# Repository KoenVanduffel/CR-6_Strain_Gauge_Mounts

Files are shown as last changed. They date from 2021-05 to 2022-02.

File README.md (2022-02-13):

- [Creality CR-6 SE & MAX extruder and hotend collection mounting directly to the strain gauge](#creality-cr-6-se---max-extruder-and-hotend-collection-mounting-directly-to-the-strain-gauge)
  * [Daughterboard](#daughterboard)
  * [fan mount](#fan-mount)
  * [Extruders:](#extruders-)
    + [Orbiter **V1.5**:](#orbiter---v15---)
    + [Mjolnir:](#mjolnir-)
    + [Bondtech LGX Lite:](#bondtech-lgx-lite-)
  * [Hot ends:](#hot-ends-)
    + [Dragon](#dragon)
    + [Mosquito](#mosquito)
    + [MicroSwiss for Creality CR-6](#microswiss-for-creality-cr-6)
    + [Stock hotend](#stock-hotend)

# Creality CR-6 SE & MAX extruder and hotend collection mounting directly to the strain gauge

## **I am in the process of moving this repo over to the PrusaPrinters.org repository of prints, for the latest updates please check the https://www.prusaprinters.org/social/211289-k2van/collections/114416 collection page. I link the relevant page in every subdirectory.**

A collection of hot end and extruder combinations for the Creality CR-6 SE and CR-6 MAX is provided in this repo.

```For ease of use the structure has been changed with every possible hotend in a directory followed by directories with the different extruders.```

All extruder / hot-end combinations are mounted directly onto the strain gauge without any connection to the carriage. The aim is to avoid the issue of the extruder pushing down on the strain gauge and causing variation in layer height in the typical gantry mounted direct drive setups. An added benefit is that the mount will prevent the strain gauge from vibrating as it blocks downward movement. Only the upward movement to enable bed measurement is allowed. Mounting the extruder this way ensures the shortest possible filament path which is exactly the aim of a direct drive setup. Only the Hemera and alike designs achieve even shorter filament paths.

There are a few gantry mounted direct drive setups available that try to avoid this pushing down on the strain gauge issue by installing a washer.

The disadvantage is that the stock hot end cover does not fit any longer (A series is planned which will work with the stock hot end cover, however the filament path will inevitably be slightly longer).

## Daughterboard
The daughterboard needs to be mounted on its own mount as the stock mount interferes with the extruder. A separate mount can be found in the daughterboard directory. 3 versions are available: one to mount the PCB directly to the mount (on standoffs) and two others that allow/require you to use the plastic OEM mounting plate/cover to mount the board to the plate.  The first mount places the board too low for the LED to safely clear your models and bed clips.
NOTE: Whichever of these daughterboard mounts you use, the LED will no longer be positioned to shine below the nozzle unless you design and make your own modifications to address that.

## fan mount
A series of fan mounts using generic 5015 or 5020 blower fan mounts optimized for each hotend is provided. With thanks to Alex for the idea of the "ears" the fan shroud design has been greatly improved and cooling efficiency of this 5015 fan is very high (enabling lower speed / quieter operation).
The fan mount has to be printed in PETG, ASA, ABS PCTG or another higher temperature filament. PLA will simply melt as its too close to the hotend.

## Extruders:
For this principle to work we need an extruder that has less than 9 mm space needed behind its filament path or it will not fit between the gantry and the hot end entrance. Two extruders have been selected:
### Orbiter **V1.5**:
> The Orbiter is the highest performing extruder I have tested. With PETG in combination with a high flow Dragon I get up to 600 mm3/min (or 25 mm3/s) extrusion speed with just 1.5% deviation versus no resistance at all.
>The Orbiter has a high gear ratio which is beneficial for extrusion as it will improve acccuracy significantly. It has been found that this can cause noise when using the filament unload function of the Community Firmware. The speed is set so high that the extruder will run at nearly 800 rpm. This will not damage the motor but some people have reported that it makes a lot of noise (probably skipping of the motor).

### Orbiter **V2.0**
>The Orbiter V2.0 is currently NOT supported! It might be an upgraded extruder versus the V1.5 however it does not fit on the strain gauge. The drive gears have been turned around which makes it collide with the back carriage plate.

### Mjolnir:
> An extruder using the internals of a BMG extruder. For this any BMG extruder or clone can be used. Also a set of the internals of a BMG extruder is sufficient. The performance is similar to a genuine BMG extruder or its clone variant. I measured an extrusion drop of 5 to 6% with PETG in identical circumstances and filament as the test with the Orbiter. Not as good as the orbiter but still more than sufficient for standard or even slightly higher print speeds.

### Bondtech LGX Lite:
> The all new Bondtech LGX Lite extruder (NOT THE REGULAR LGX, that one too bulky to fit the CR-6). A mount is modeled but untested for now as I do not own an LGX lite. This could well become the highest performance option as its lighter and more compact than the Orbiter 1.5 and  can be mounted closer to the strain gauge bringing the center of mass of the whole hotend assembly closer to the strain gauge thus avoiding vibration of the strain gauge upon higher accelerations.
> Extrusion performance is obviously untested by me but should be equal to or better than the Orbiter.

## Hot ends:
The hot ends chosen all have mount screw holes on the top making them rather easy to mount. Also are they significant all metal upgrades to the stock hot end.
The extruder - hotend mount blocks can be printed in any filament however PETG, PCTG, ASA or ABS are preferred over PLA.

### Dragon
> both high flow and standard flow

### Mosquito
### MicroSwiss for Creality CR-6
### Stock hotend
<br/>
Just a couple of examples:

<img src="images/README/CR-6 Dragon & Orbiter mount with stator fan.png" alt="CR-6 Dragon & Orbiter mount with stator fan" width="60%" />

![CR-6 stoch hotend and Mjolnir extruder](https://user-images.githubusercontent.com/13643644/121425564-d613ab00-c972-11eb-9b16-f10bbce3bcb8.png)

![Mosquito   Orbiter mount 2](https://user-images.githubusercontent.com/13643644/121426032-65b95980-c973-11eb-9b75-b8b25f1e59a7.png)

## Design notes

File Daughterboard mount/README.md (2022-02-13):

### Updated daughter board mount and ribbon cable management

The daughterboard mount  and ribbon cable holders can now be found on PrusaPrinters.org

[PrusaPrinters](https://www.prusaprinters.org/prints/126838-cr-6-direct-drive-dragon-hf-sf-and-orbiter-v15-mou)

The original hot end cover and daughter board mounts are not useful any more as the extruder & hot end mounts come in the way (except for some of the Bowden setup's). Therefore these companion daughter board mounts and cable management have been made. 


The updated mount supports the whole board and has a clamp to hold the lowest rather flexible part of the ribbon cable. This works in conjunction with  the ribbon cable clamps and ribbon cable holder (which clips over the pulley housing of the X-axis motor).



For the daughterboard mount there are additional options. One to mount the with the original plastic back to enable the use of the blue LED. and one with a right angled approach to enable easier cable management (requires somewhat longer than stock heater and thermistor wires). The daughter board mount V1.1 (still available) was only a small mount just enough to hold eth daughter board in place.

The part fan shroud has been moved out of this directory into the different hot end directories. The different sizes of heater blocks ask for slightly different designs for the different hot ends.

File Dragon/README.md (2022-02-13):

# Dragon hotends

The Dragon hotend designs including the daughterboard and part fan shourds for the Orbiter have been moved to the PrussaSlicers page.

[PrusaPrinters](https://www.prusaprinters.org/prints/126838-cr-6-direct-drive-dragon-hf-sf-and-orbiter-v15-mou)

**The Dragon Orbiter V1.5 has been updated to fit both the high and standard flow version. The older version is still available in the high flow and standard flow directories.

The latest V4 mount for Dragon + Orbiter V1 now has a connection of top and bottom on the left side making the mount even more sturdy and probably more durable. A small cutout has been added to grant access to the screw of the daughterboard mount for ease of maintenance.
These updates are to be ported to the other designs soon.**

The Dragon hotend (TriangleLabs and Phaetus version are nearly identical and fit both) has a strong reputation of being a reasonably priced high qualtiy hotend. Personally i prefer the high flow version as it hasn't shown any of the disadvantages sometimes attributed to a high flow hotend but does have the advantage of being capable of melting a lot of plastic.

# Part fan shrouds

The part fan shroud in this directory fits all extruder versions, high flow as well as standard flow.

2021-11-28 update: 
5015 and 5020 versions of the fan shroud are now available
The "ears" have been opened up as it was found not needed to close as much as earlier versions did. This further improves cooling efficiency.
A secondary channel pushing some air directly downwards below the fan shroud has been added as this region was getting less cooling thus fixing the reduced overhang capability in that region.

CR-6 5020 part fan shroud

CR-6 5020 part fan shroud 2

CR-6 5020 part fan shroud 3

CR-6 part fan shroud simulation

On the 2 section analysis the internal flow redirector is visible. A blower fan typically gives a higher output flow towards the circumference versus the inside The devider helps correcting that. The second divider lets some air flow to just below the shroud as this area gets too short cooling time when the hotend moves to the left.

The simulation picture shows the effect ot the ears in avoiding a "shadow" directly to the left ot the nozzle. Basically they make the airflow converge again.

I ran the Teaching tech 4-way overhang test to validate my design: https://www.thingiverse.com/thing:3167063





This test produces overhangs up to 80°. Up to 60° the overhangs are perfect, 70° is perfectly useable and even 80° would be useful if no other way is found and some sagging is accepted (PLA @200 °C, 0.4 mm nozzle, 0.2 mm layer height, 0.45 mm line width, 25 mm/s exterior walls). I tested slower print speeds but that produces lesser results. Using the 5015 the results are less good when printing faster. The 5020 manages up to 50 mm/s with no/barely loss in overhang quality. Beyond 50 mm/s outer layer speed a 10° lesser overhang maximum should be used.

### Print settings:

- layer_height = 0.2
  layer_height_0 = 0.24
  line_width = 0.45
  infill_line_width = 0.4
  
  bottom_layers = 5
  top_layers = 5
  wall_line_count = 5
  
  material_bed_temperature = 85
  material_print_temperature = 230
  
  infill_pattern = gyroid
  infill_sparse_density = 20
  
  cool_fan_speed = 40
  cool_fan_speed_max = 75
  cool_min_layer_time = 10
  cool_min_layer_time_fan_speed_max = 20
  cool_min_speed = 10
  
  z_seam_corner = z_seam_corner_weighted
  z_seam_type = back
  z_seam_x = 235

Adjust temperature and fan setting if using another filament than PETG

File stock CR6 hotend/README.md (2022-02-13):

The stock CR-6 hotend and Orbiter design can now be found on PrusaPrinters.org.

[PrusaPrinters](https://www.prusaprinters.org/social/211289-k2van/collections/114416)

The part fan cooling mount featured here is compatible with both Bowden and direct drive setup.

Last modification adds a small cutout because some 5015 fans have rather large clips to close the body that were interfering with the mount.

CR-6 part fan mount stock hotend v3

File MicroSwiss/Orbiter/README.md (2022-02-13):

# MicroSwiss and Orbiter

The mount has been moved to PrusaPrinters.org. The new version is identical to the one for the stock hotend.

[PrusaPrinters](https://www.prusaprinters.org/prints/132112-cr-6-direct-drive-stock-or-microswiss-hotend-orbit)

This mount is menat to install the Orbiter extruder and MicroSwiss CR-6 hotend in direct drive mode directly onto the CR-6 SE or CR-6 Max strain gauge.

There is not hotend in the render file as MicroSwiss hasnt released a CAD file of the extruder. If anyone has a CAD file please notify me so I can integrate it in the render for convenience.

Many thanks to @ritchiedc on the CR-6 discord for providing me the necessary measurements to adapt the existing mounts to the MicroSwiss hotend.

CR6 MicroSwiss hotend and Orbiter extruder mount v1

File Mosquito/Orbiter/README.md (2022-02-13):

# The Mosquito plus Orbiter mount direct to the strain gauge

The Mosquito and Orbiter mount has been moved to PrusaPrinters.org

[PrusaPrinters](https://www.prusaprinters.org/prints/129781-cr-6-direct-drive-mosquito-standard-and-magnum-and)

CR6 Mosquito and Orbiter mount on the strain gauge

The mount for the Mosquito - Orbiter combination to the strain gauge. The file marked injection molding inserts is meant to be used with the typical IM inserts. The preferred inserts are the regular hot melt inserts as they give a much stronger part.

The regular 5015 part blower fan mount does not fit! A modified version to fit the wide Mosquito heater block is incuded here.

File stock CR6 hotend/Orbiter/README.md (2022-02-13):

# Mount block to mount the Orbiter extruder to the stock CR-6 hotend.

The stock CR-6 hotend and Orbiter design can now be found on PrusaPrinters.org.

[PrusaPrinters](https://www.prusaprinters.org/social/211289-k2van/collections/114416)

CR6 stock hot end and Orbiter extruder mount v1

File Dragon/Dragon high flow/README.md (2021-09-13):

# Dragon high flow hotends
The Dragon high flow hotend (TriangleLabs and Phaetus version are nearly identical and fit both) has a strong reputation of being a reasonably priced high qualtiy hotend. Personally i prefer the high flow version as it hasn't shown any of the disadvantages sometimes attributed to a high flow hotend but does have the advantage of being capable of melting al lot of plastic.

There are 3 extruder options:
* Bowden setup
* Orbiter **V1.5** (high performace large gear extruder)
* Mjolnir extruder (3d printed BMG clone)

A version using the Voron Galileo Clockwork extruder is in the planning. The Galileo Clockwork uses the internals of the Orbiter and will thus perform very similar.

`There have been multiple requests to make a Bondtech LGX or Superfly version. These extruders are however too bulky and simply don't fit in the space available. To mount these they have to be lifted over the carriage back plate which will increase vibrations as the momentum on the strain gauge is increased.`

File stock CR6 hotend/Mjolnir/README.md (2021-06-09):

CR-6 stoch hotend and Mjolnir extruder

Mount the Mjolnir extruder directly on the CR-6 SE and MAX hotend.

There are 2 "front" files. One has a flat bottom, the other one an extension to guide the Bowden tube. Please try what suits best.

The Boden tube length will be critical as it has to press down on the hot end to avoid cloggs but not too much so as not to deform and cause a restriction to the filament path. The Bowden tube should be 55 mm.

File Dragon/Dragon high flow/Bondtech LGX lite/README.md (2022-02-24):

# Bondtech LGX Lite & Dragon high flow
This mount has been updated and moved to PursaPrinters.org:
https://www.prusaprinters.org/prints/137422-cr-6-direct-drive-lgx-lite-and-dragon-mount-to-the

LGX lite Dragon

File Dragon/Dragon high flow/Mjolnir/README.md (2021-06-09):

cr6 Mjolnir extruder Dragon v1

The Dragon extruder is a popular after market all metal extruder. This page host the mounts to combine the Dragon with the Mjolnir extruder (Bondtech BMG derivative).

Needed parts:
 Dragon hotend: 
   https://nl.aliexpress.com/item/1005002629698126.html
   BMG extruder internals:
    https://nl.aliexpress.com/item/4000021186440.html
Both the extruder and the hotend are available from different sources as well. Watch out there are some Dragon clones where the top BMG mount cannot be removed. These will not fit.

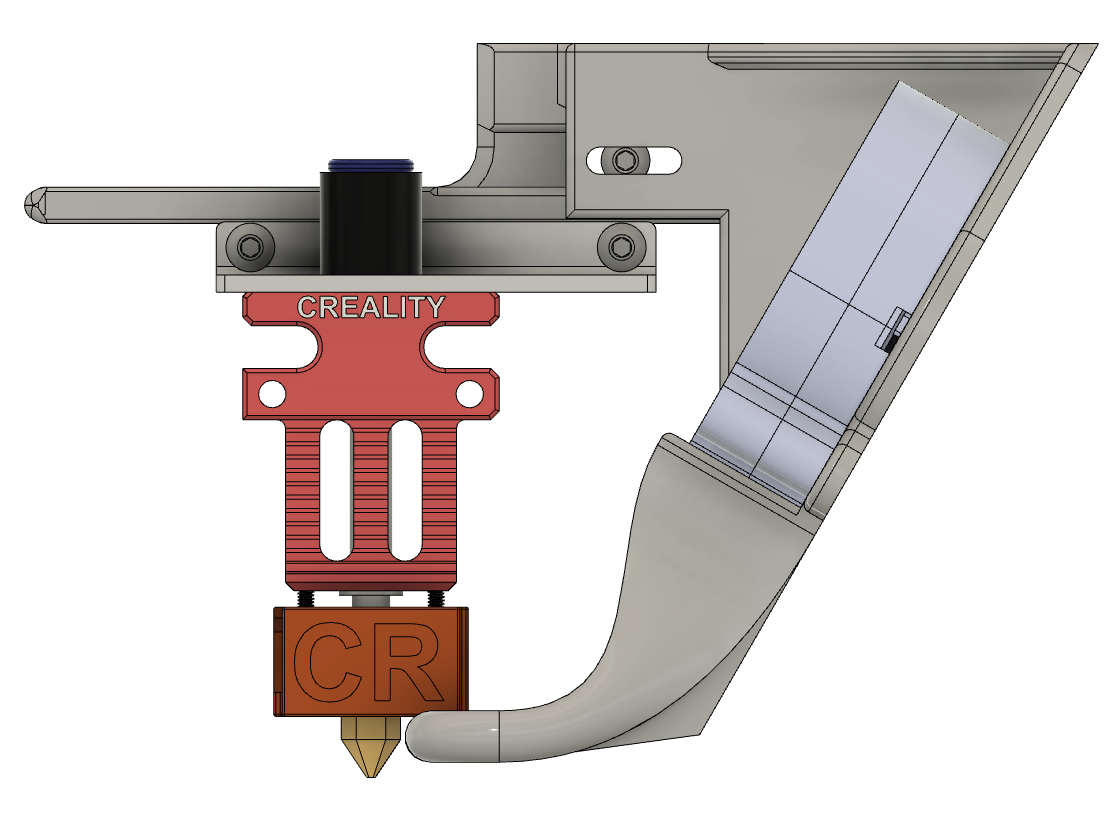
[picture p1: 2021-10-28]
stock CR6 hotend/images/README/CR-6 part fan mount stock hotend v3.png

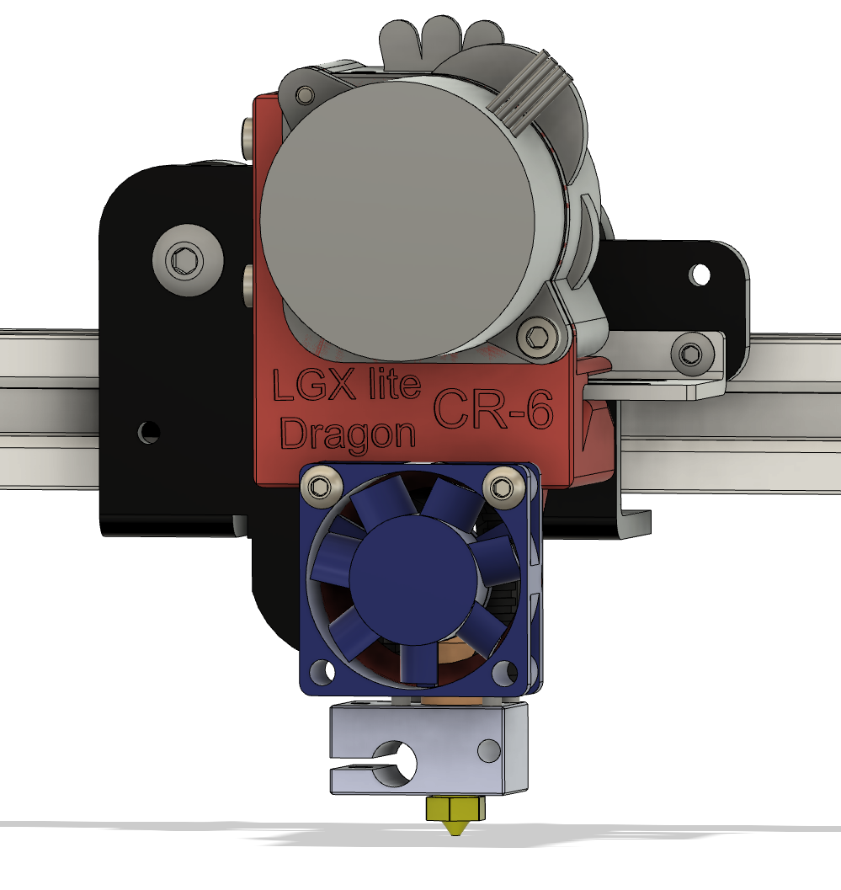
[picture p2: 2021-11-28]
Dragon/Dragon high flow/Bondtech LGX lite/LGX lite & Dragon.png

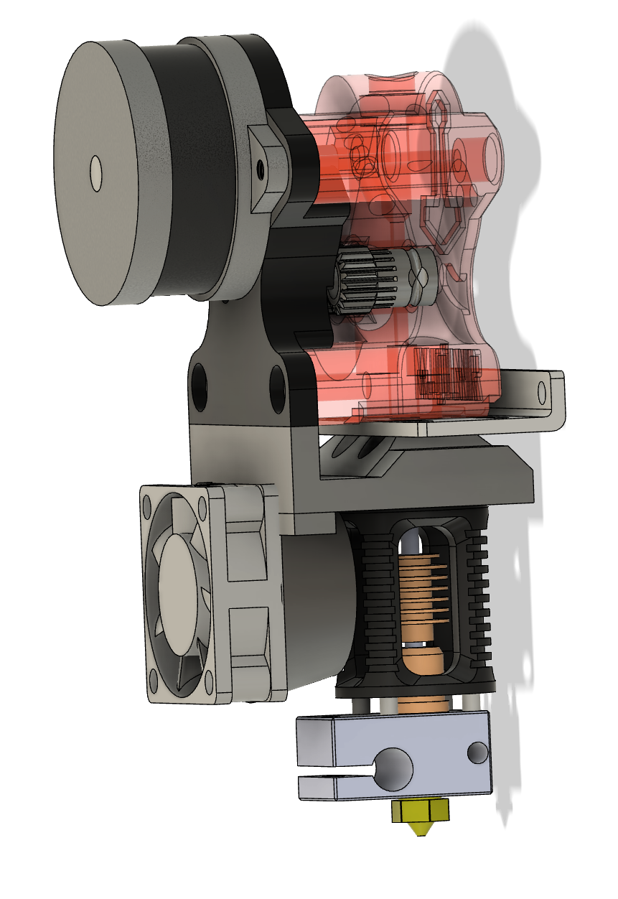
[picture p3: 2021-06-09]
Dragon/Dragon high flow/Mjolnir/cr6 Mjolnir extruder & Dragon v1.png

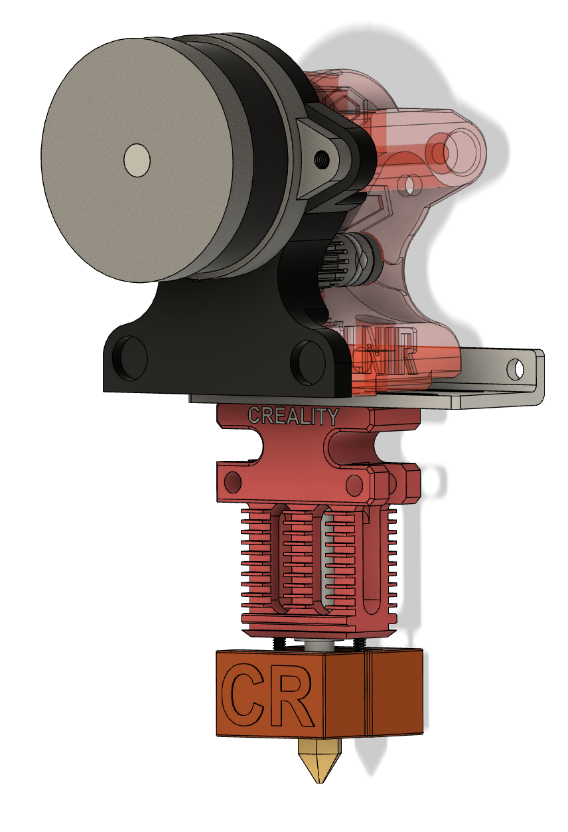
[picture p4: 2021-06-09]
stock CR6 hotend/Mjolnir/CR-6 stoch hotend and Mjolnir extruder.png

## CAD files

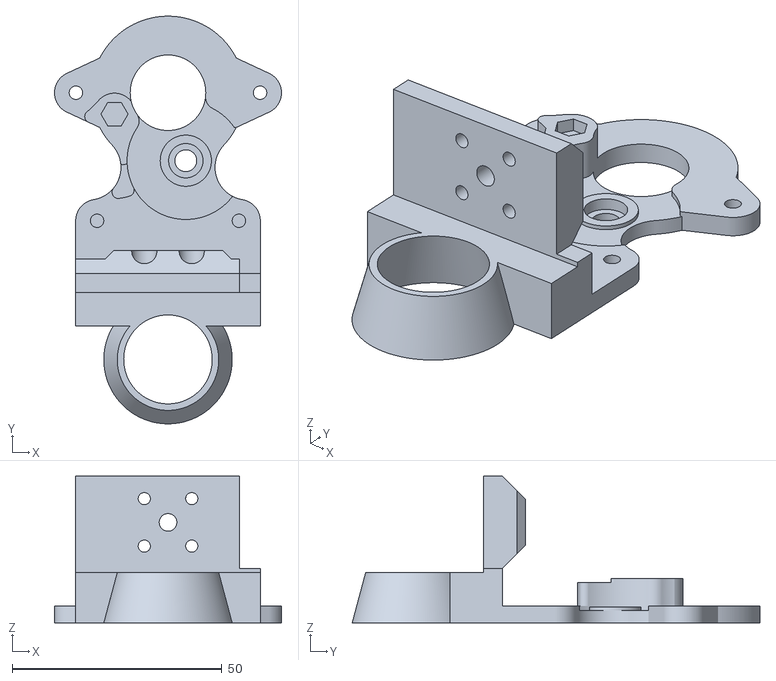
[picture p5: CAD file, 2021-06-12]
Dragon/Dragon high flow/Mjolnir/CR-6 Dragon standard flow & Molnir extruder M3 4.6mm hot melt inserts back.stl
54.1 x 97.2 x 35.0

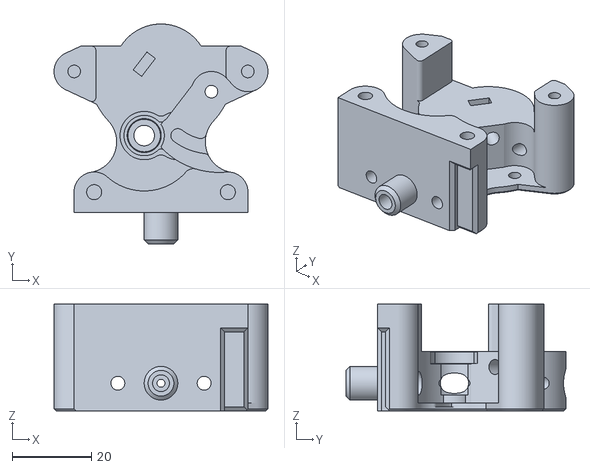
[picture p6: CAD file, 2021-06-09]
stock CR6 hotend/Mjolnir/CR-6 stock hotend and Mjolnir extruder front with filament path.stl
54.1 x 55.6 x 27.0

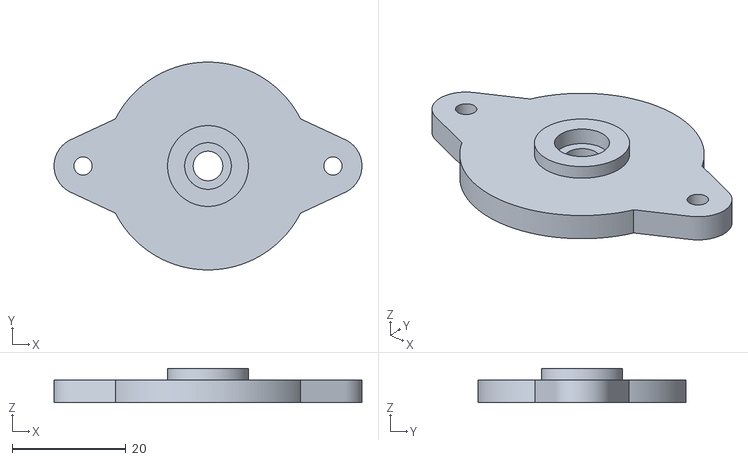
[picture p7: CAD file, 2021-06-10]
Dragon/Dragon high flow/Mjolnir/Motor Dummy_1x_SN.stl
54.1 x 36.5 x 6.00

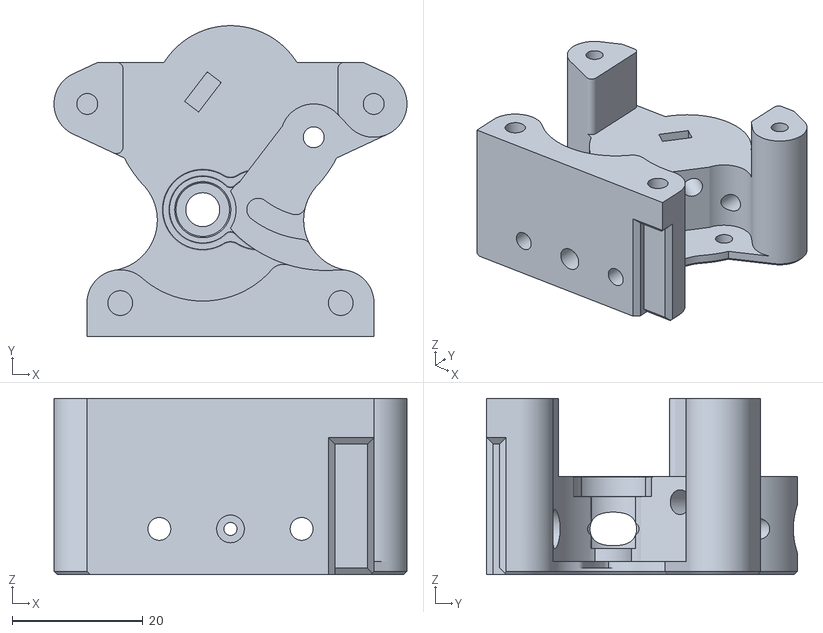
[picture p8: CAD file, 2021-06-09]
stock CR6 hotend/Mjolnir/CR-6 stock hotend and Mjolnir extruder.stl
54.1 x 47.6 x 27.0

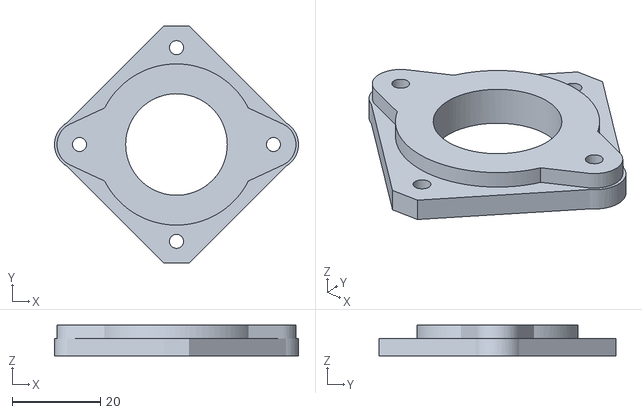
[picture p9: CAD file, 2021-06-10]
Dragon/Dragon high flow/Mjolnir/Nema 17 adapter.stl
55.2 x 53.7 x 7.00

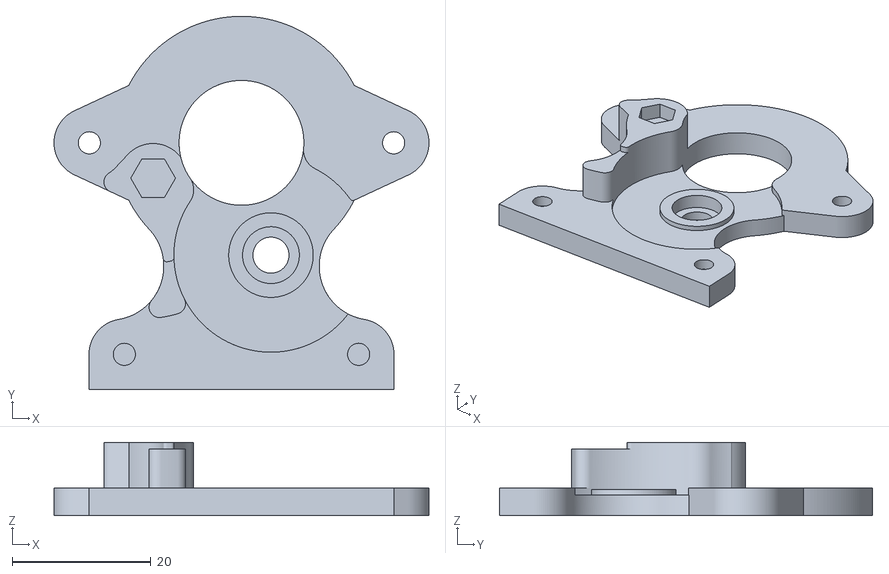
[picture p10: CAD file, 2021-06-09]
stock CR6 hotend/Mjolnir/CR-6 stock hotend and Mjolnir extruder back.stl
54.1 x 53.9 x 10.6

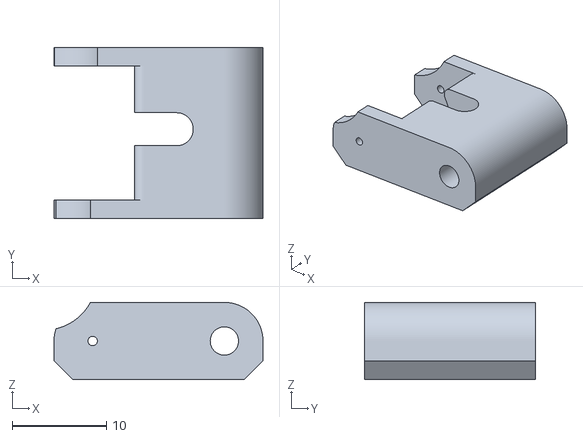
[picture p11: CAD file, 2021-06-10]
Dragon/Dragon high flow/Mjolnir/31_mjolnir lwx latch_1x_SN_BN.stl
22.2 x 18.2 x 8.20

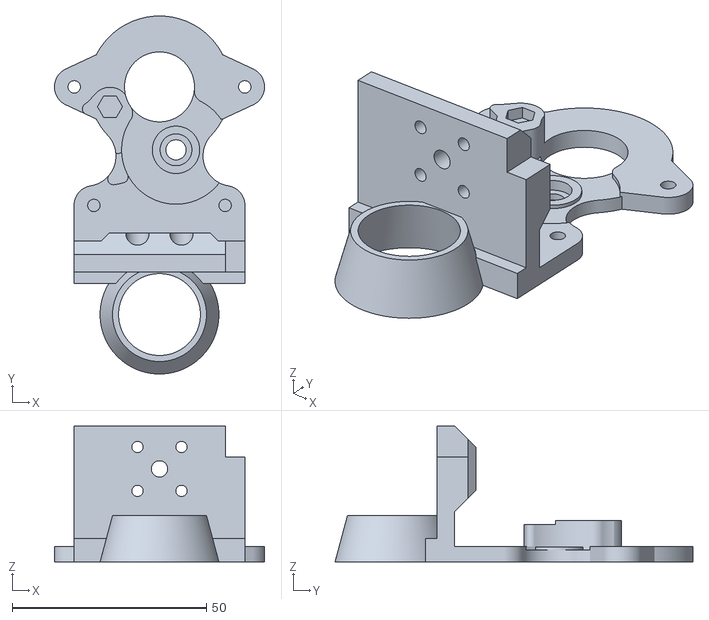
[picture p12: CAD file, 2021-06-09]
Dragon/Dragon high flow/Mjolnir/CR-6 Dragon high flow & Mjolnir M3 4.6mm hot melt inserts back.stl
54.1 x 92.2 x 35.0

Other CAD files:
Dragon/Dragon high flow/Mjolnir/CR-6 Dragon & Mjolnir hot melt inserts front.stl

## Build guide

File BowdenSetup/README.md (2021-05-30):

# Creality CR-6 SE and CR-6 MAX Bowden mounted Dragon hotend.

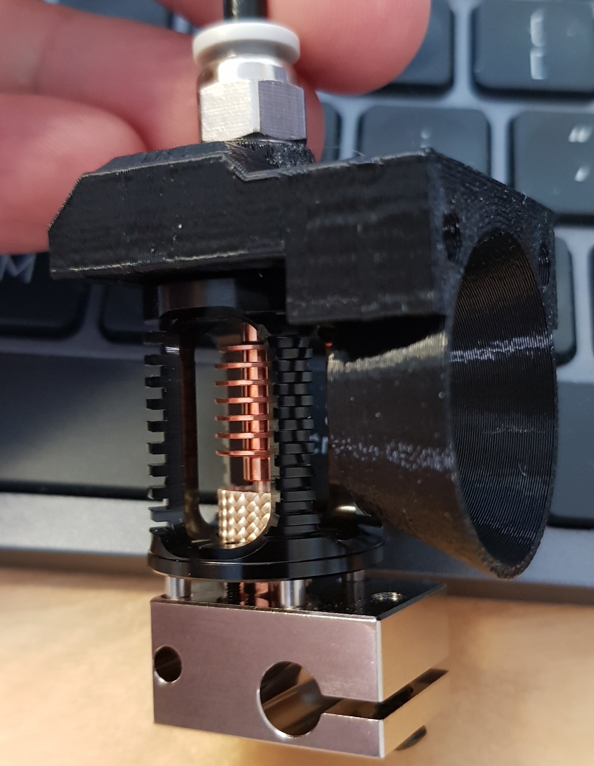
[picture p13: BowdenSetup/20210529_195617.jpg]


## 4 variants are available:
	
	High flow Dragon with the fan shroud slightly higher mounted to avoid cooling the extended heatzone
	Standard flow Dragon with fan shroud mounted lower
	
	For both versions there is a choice between a version with:
    M3 bolts and nuts
    M3 bolts and hot melt inserts. For the fan 2 3mm long M3 hot melts are sufficient,
		longer is possible. For the mount to the strain gauge 7 mm long M3 hot melts are recommended.

### Print prefereably in PETG or other high Tg material. The bottom of the fan shroud might sag when printing in PLA.

## Printing:

	0.16 mm layer height
	activate "Use Adaptive Layers" with maximum variation and step size 0.04 mm and Topography size 0.2 mm
	0.44 mm line width
	4 walls, top and bottom layers
	Activate "Alternative Extra Wall" in the walls menu of Cura
	20% Gyroid infill (Gyroid provides good vibration damping)
	No supports, the holes and screw tread print good enough on my CR-6
	Print at high temperature (240 or 245 °C for PETG)
	You might ocnsider upping the flow rate to 105% to get maximum part strenth. Experiment with this setting if needed.

## Mounting:
	
	Mount the Dragon with the supplied bolts
	Mount the fan with 16 or 18 mm M3 bolts
	Mount the assembly to the strain gauge with 10 mm M3 bolts
	
	The 10 mm Bowden coupler is screwd directly in the platic thread. Do not overtighten!

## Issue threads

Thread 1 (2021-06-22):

How to connect the mosquito to your design?

deuse-x, 2021-06-22:
Hi.
I just made your great design for the CR- SE Mosquito_And_Orbiter

I think I will have to buy some inserts to connect it to the strain gauge.

But I can not find a way to connect the Mosquito to your design.
The holes for it are way to big.
I can't put a insert in.
Can you help please?

Thank you for your design and letting us use them.

KoenVanduffel, 2021-06-22:
Both sets of holes should get melt inserts. I will check whether I made a mistake in the sizing.

I don't own a Mosquito (clone) myself so haven't been able to test it.

⁣Get TypeApp for Android

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

deuse-x, 2021-06-22:
> Both sets of holes should get melt inserts. I will check whether I made a mistake in the sizing. I don't own a Mosquito (clone) myself so haven't been able to test it. ⁣Get TypeApp for Android
> […](#)
> On Jun 22, 2021, 15:39, at 15:39, deuse-x ***@***.***> wrote: Hi. I just made your great design for the CR- SE Mosquito_And_Orbiter I think I will have to buy some inserts to connect it to the strain gauge. But I can not find a way to connect the Mosquito to your design. The holes for it are way to big. I can't put a insert in. Can you help please? Thank you for your design and letting us use them. -- You are receiving this because you are subscribed to this thread. Reply to this email directly or view it on GitHub: #1

Thank you.

I just bought these  https://www.amazon.co.uk/threaded-embedment-assortment-ultrasonic-embedding/dp/B08KVWYTN1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

Hope they are the right kind.
I will post pics.

Thank you again

KoenVanduffel, 2021-06-22:
These are not actually hot-melt inserts but injection molding inserts (they often get sold as hotmelt inserts unfortunately). You can either get the real ones (these are the ones I bought https://nl.aliexpress.com/item/1005001553234012.html) or i adjust the hole sizes but that will be tricky as there is very little room to the filament path. Hence If you reprint you will probably have to drill the filament hole to get the Bowden tube trough.
I have a set of the ones like you bought, they don't have M2.5. However if extrapolating from the M2 the shaft of the M2.5 ones should be 3.3mm. The holes are 3.2 and print 3.0 (due to the molten plastic moving inward a little). If you happen to have a 3.2 or 3.4 mm drill you could increase the hole size a little.
I uploaded a version with the increased hole size to accommodate the IM inserts. I have not increased the size of the holes for the Orbiter or strain gauge as those seem to be a bit more size tolerant when I understand you correctly.
I will include a bit more text and a video from CNC Kitchen to explain this better.

deuse-x, 2021-06-23:
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

Thank you so much.

I just bought the ones from AliExpress.
It's the 300 set I got.

KoenVanduffel, 2021-06-23:
I don't have a real YouTube channel. I just posted a 10:24 Benchy today which is my first ever YouTube post https://m.youtube.com/watch?v=kOTIyuHyYVc

deuse-x, 2021-06-23:
> I don't have a real YouTube channel. I just posted a 10:24 Benchy today which is my first ever YouTube post https://m.youtube.com/watch?v=kOTIyuHyYVc
> Quality is quite poor as it was just the Raspberry cam recording it...

WOW that does move fast!!!

Never seen anything like it  :)

Well done dude.

deuse-x, 2021-06-23:
> I don't have a real YouTube channel. I just posted a 10:24 Benchy today which is my first ever YouTube post https://m.youtube.com/watch?v=kOTIyuHyYVc
> Quality is quite poor as it was just the Raspberry cam recording it...

Sorry to bother you.

But which set did you buy off aliexpress?
I know nothing about these. I've just noticed that there are all lengths and sizes.

Thanks again.

KoenVanduffel, 2021-06-23:
When I bought them i didn't know anything either :). I bought set nr 4-20 which I though were the sizes I would use most. i bought a larger bag of M3x4.5x3.0 and M3x4.6x7.0 from this seller (watch out he also has M3x3x4.2 so the same screw thread but smaller outside diameter, in itself no issue but you need to make the holes the correct size) https://nl.aliexpress.com/item/4000958639502.html
There are however quite a lot of sellers, probably also local ones. the thing to watch out for is the narrower tip and 2 rings with angled nudges. The IM ones have straight nudges which is OK but they are at the sides which makes mounting difficult and pushed the plastic in front if you push then in too quickly. So be slow, let the plastic melt and gravity should do the work.

deuse-x, 2021-06-23:
> When I bought them i didn't know anything either :). I bought set nr 4-20 which I though were the sizes I would use most. i bought a larger bag of M3x4.5x3.0 and M3x4.6x7.0 from this seller (watch out he also has M3x3x4.2 so the same screw thread but smaller outside diameter, in itself no issue but you need to make the holes the correct size) https://nl.aliexpress.com/item/4000958639502.html
> There are however quite a lot of sellers, probably also local ones. the thing to watch out for is the narrower tip and 2 rings with angled nudges. The IM ones have straight nudges which is OK but they are at the sides which makes mounting difficult and pushed the plastic in front if you push then in too quickly. So be slow, let the plastic melt and gravity should do the work.

I will get the 4-20 one for starters.

I'm old and my mind is not working right  :)
So sorry about all this.

KoenVanduffel, 2021-06-23:
No problem, this also teaches me where i can improve if only in the explanation part (which i still have to make for the biggest part anyway).

Closed 2021-08-24.

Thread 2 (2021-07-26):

Not really an issue. Can I confirm the strain gauge still functions?

RobboCop, 2021-07-26:
Hi,

Sorry for making this an issue, I don't have much experience on GitHub, so I didn't know another way to ask this question.

From what I can see of the CAD, the mount will surround both sides of the strain gauge. I am guessing that this would render the strain gauge redundant? It's possible that you have allowed sufficient room for the gauge to still function, but I can't tell from just eyeballing it.

Further, your speed boat video starts after the homing process has been completed, so I couldn't tell from that.

The video was impressive though! Did you need to add active cooling for the stepper motors? I know that some people have complained that theirs get quite hot.

ritchiedc, 2021-07-26:
The strain gauge still functions. The mount does restrict the gauge from deflecting down by design but it still deflects upward when the nozzle contacts the bed.

KoenVanduffel, 2021-07-26:
Thx Ritchie, I can't explain the principle any better. Blocking the downward movement is the aim of the design as it dampens vibration. The upward movement is left free for the bed measurements to function indeed.

KoenVanduffel, 2021-07-26:
I didn't comment on the motors. I use a BTT board and Klipper sets a lower current when not moving which keeps the motors much cooler. The  move current was increased to 1A, hold 350mA for the Y axis and 850mA 350mA for the X axis respectively.

RobboCop, 2021-07-26:
Thanks for the replies gents, that was the news I was hoping for.

Yes there are several separate mods just to prevent the strain gauge moving down to stop the hot end from oscillating/bouncing. So that is a feature really, just couldn't tell if it would still deflect upwards.

Looks like I have some parts to buy then. I got a Prima all metal hot end, but the actual hot end is fastened to the heat break with a tiny grub screw. Applying practically any torque to the steel grub screw simply strips the thread from the alloy heat break... Looks like the micro swiss design is very similar, so I don't really want to buy another setup and be faced with the same issue. Thinking I might just go all in and opt for a setup similar to yours

KoenVanduffel, 2021-07-26:
I have no experience with the prima3d or MicroSwiss hotends. They both seem to perform well in printing but might have the disadvantages you describe.

I have ran the Mjolnir Dragon combintion for a while before switching to the Orbiter Dragon combination. The Orbiter extruder has more consistent flow in the higher flow ranges (less than 1% drop in extrusion up to the point where the hotend can't melt the plastic any more) compared to the BMG designs (5 to 7% drop). As long as you are not printing with large nozzles or more than 100 mm/s you won't notice this difference.

Bear in mind however that the Dragon also bas a few small screws. The screws and hotend body have however proven to be of good quality for me as I haven't damaged any of them even though I have fastened and loosened them a few douzen times when developping the mounts.

KoenVanduffel, 2021-08-24:
Clarified

Closed 2021-08-24.

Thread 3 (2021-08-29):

Heat creep with PETG

RobboCop, 2021-08-29:
**Describe the bug**
So, I have assembled this setup with a Dragon highflow and Orbiter. Works the goods with PLA ~210C, I printed the fasted Benchy that the unmodified community firmware would allow (acceleration is capped at 500mm/s/s) and it is probably the cleanest benchy I have ever printed. Happy, high fives all around. Now, I bought the printed largely to print things for my workshop and racecar, so PLA is pretty and all, but not up to scratch. The printer is still in my house and so I am saving the ASA for when I have finished building the enclosure for it in the workshop. About 15 minutes into my first PETG print, the whole thing clogs, I wasn't monitoring it and so I found it at the end. Clean stop, the last layer of infill that was printed looks quite sharp really. Anyway, I tried to manually feed filament, no good, no good with the nozzle removed... yikes. Cold pull no good. Heated back up and got a acupuncture needle through, started to feel happier, but still couldn't feed in filament. I've removed the hot end now and there is clearly a coating of hardened filament coating the outside of the heatbreak, at least part way up.

I'm guessing that the setup could handle the lower temperatures (and less fluid behaviour of PLA) but PETG not so much...

**To Reproduce**
Steps to reproduce the behavior:
1. Print PETG 250C, 0.6 nozzle, 1mm retraction @ 35mm/s, I was only printing at 60mm/s (maybe printing faster could avoid the problem?)
2. Come back later and find clog

**Expected behavior**
Hot end not jammed after print

**Screenshots**
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
Looks great, Planning on re-printing the parts in black ASA once I get onto that

**Additional context**
Unrelated, but I had to sand down the bottom of the part cooling nozzle as it was ever so slightly lower (or the same height) as the nozzle and was scraping up the prints as they were going down.

KoenVanduffel, 2021-08-29:
I have not seen heat creap before even not when printing ABS at 280 °C in my own setup or had any heat creap reports.

I print PETG between 240 and 250 (higher temperature if I need structural parts) with 0.5 to 0.7 mm retraction @60 mm/s retraction speed. Print speed is typically between 100 and 200 and acceleration 1500 to 4000 (Klipper). The higher speed might make the problem less noticeable but it would still occur imho. The 1 mm retraction you use is on the high side for a direct drive setup and could pull some molten material into the heat break.

The physical setup should not cause any issues as long as its ridged enough. Hence I don't believe the Orbiter to Dragon mount itself causes this.

Where there could be an issue is in the fan mount in combination with the fan used.  The fan shroud inlet is 29 mm wide and outlet 18 mm, maybe that is too much a squeeze for some types of fans or fans that are rotating slower. BTW the potmeter you have is that to regulate fanspeed?

I adapted the V2 design (main V2 changes: made it more sturdy and the Dragon sits 1.3 mm lower, that was a placement bug in the original version) to have a 24 mm outlet. If your fan is stalling due to the squeeze this should fix it (I can make one that does not squeeze at all if you like that better). I have uploaded it to the Dragon & Orbiter directory.

I see you are using the original part fan shroud. The latest model has improved placement and fixation and should not touch the build plate any more. The hotend will have to be turned 90° to make the ears fit. Cooling performance is improved a lot. The Dragon you have is the Phaetus one. I dont have a cad model of that one but assume the difference is only hte corners that are chamfered and not the overall dimensions.

RobboCop, 2021-09-04:
Thanks for the fast and detailed reply.

I am seriously considering the conversion to Klipper just to reap the full benefits of the parts that I have installed. I could do my own custom configuration of the community or stock firmware, but that's probably 80% of the effort for much less gain.

This is my first direct drive unit and so it is more than likely that I have too much retraction. Hopefully that is the cause of my problems. I attempted to tune stringing based off of stringing tests, but if I am honest, none of the stringing test prints I did had great results. That's how I ended up with 1mm, but I have changed it to 0.6mm now and we'll see what that goes. I would certainly prefer the problem to be my dumb settings than a heat creep issue.

The potentiometer I have on the side doesn't regulate fan speed but is just the CHEP fan mod. It just disables the hot end fan when the hot end is below ~50C. I suppose it's not impossible that it might be stealing a tiny amount of current when the fan is at full song, but the transistor should just be acting as a relay so I am guessing it would be negligible. The fan itself is the factory unit. It is completely possible that it isn't up to the task with the upgraded parts, but I would think that this would only be the case when running the kinds of speeds/accel that you are running, rather than the speeds that I am currently stuck at, which aren't really that much more than the factory unit is capable of. Also, I would have thought that there was more headroom in the PID tuning...

I thought I had the latest version of all of the parts, but I guess I must have missed some updates. As I said in my original post, I am planning on re-printing in black ASA once I build an enclosure for the printer and move it to my shed, so I will get the latest versions of the files then.

I managed to clear the jam in hot end just by using a heat gun and warming up the entire thing. Once it was hot I gently pushed a 1.5mm drill bit through the unit and that cleared the vast majority of the plastic. I believe I got the rest after I reassembled it and heated the whole thing to 260 and extruded a bunch of plastic through. For now I am not going to print any PETG if I can avoid it and will hopefully be able to solve all of the other issues with the new ASA setup and tuning.

Once again, thanks for your advice and continued development of the parts.

KoenVanduffel, 2021-09-05:
About the CHEP fan cut-off: I haven't seen the circuit but if its a transistor it steals 0.7V. Thats quite neglectable on the 24V power supply. I use the stock 3010 as well so that should be OK. You might have seen I made a version that doesn't close as much that should be much less sensitive.

As to Klipper you can find my setup in the other GitHub repo. Setting up Klipper from scratch (well the sample files in the main Klipper repo)  was a bit of a steep learning curve as those are not quite complete. I tried to have complete setups for all 3 the boards on the GitHub.

KoenVanduffel, 2021-09-08:
Hi, After your report I did do some further investigation and found that I can induce heat creep by slowing down the fan just a little (20V instead of 24V power supply is what I tested). This means the shroud indeed closes too much and I was just lucky till now not to get heat creep.

There is already a quick and dirty design with an increased fan outlet which i will replace with a polished up design today.

A little info to the history: In the first iteration i had a shroud opening of 20mm this has not caused issues (at least not to my knowledge), the design you used has an opening of 18mm. i tested that with the stock fan and a Sunon both were working fine. However when the stock fan has a reduced voltage it (partially) stalls. Hence this narrowing of the shroud is too close to what the fan can provide in pressure. To stay far away from the point where issues occur i have made the revised design with a 24mm outlet.
The reason to narrow the outlet is not to blow too much air over the heater block and the extended melt zone coming up from the heater block. I will run a few tests with a stator inside the fan shroud to try and eliminate this stalling. There are a few videos that show what can happen to a centrifugal fan + duct, can't find back the one i was looking for but this one shows it too: https://www.reddit.com/r/3Dprinting/comments/7sqzw4/heres_what_happens_when_you_put_a_duct_on_an/ here is another one: https://www.youtube.com/watch?v=rDq4KSlZcTo&t=7s

RobboCop, 2021-09-09:
Thanks for investigating further. I am planning on re-printing the supports once I have my enclosure built and so I will definitely print the other version when I get there. Unfortunately, I have to finish the custom lower cabinets the enclosure is going to be sitting on first, so not something I am expecting to get done overnight.

I was also considering replacing the stock heater block fan with something designed for PC watercooling or something to get some more static pressure. I just doubt there would be any watercooling gear that small. Maybe something for cooling like an industrial rack mounted server or something? I mean, next to that 5015 axial fan, noise isn't an issue anyway.

KoenVanduffel, 2021-09-13:
Both for the Dragon high flow and Dragon standard flow new versions of the mount block with integrated fan stator to vastly improve air flow have been uploaded. Feel free to upgrade to this version.

Closed 2021-09-13.

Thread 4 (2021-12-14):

MicroSwiss Fan Mount / Daughterboard Mount

leesafur, 2021-12-14:
The MicroSwiss fan mount hits the X axes tensioner end piece but still passes by. Probably only 1mm of clearance is need to solve this. It also has the same issue as the last modification to the stock hotend. Where a small cutout was added because some 5015 fans have rather large clips to close the body that were interfering with the mount. Would also like to request that the 2-M5 holes for the fan mount resized smaller. This will allow us to omit the nuts currently needed and help reduce moving mass. It would be nice to see it lightning up significantly as this part is huge and adds a lot of weight to move around. lol cable clips added to hold the fan power wires would be great too.

If we reduce the 2-M3 hole sizes on the daughterboard we can omit the currently needed M3 nuts. Also if you look at the photo, you can see that the daughterboard could use slightly more clearance from the extruder tensioning nob. It could also use some sort of cable strain relief.. I tried designing one but I suck at it.. Take a look at the zipped STL. The idea was to keep it light and it did work but was to flimsy.

First time posting something like this... I apologize in advance if this is the wrong way to report my findings.
Thanks
Lee

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
[Daughter Board.zip](https://github.com/KoenVanduffel/CR-6_Strain_Gauge_Mounts/files/7712281/Daughter.Board.zip)

KoenVanduffel, 2021-12-18:
Well I am not too processioned on GitHub either so that first time posting is surely OK :).

You point out a few issues that are tough to improve. The daughterboard can hardly be moved as the stock thermistor cable is too short and if I move it backwards it will collide with the X endstop (I had it a few mm further originally but didn't work.
The lever of the extruder I never use, I just use the load and extrude feature of the firmware.

The fan mount touching the X-tensioner was a problem I though to have solved but apparently there are cases where the clearance still isn't enough. I will add a little more in the next revision.

As tot he weight I am still developing/finetuning  the shroud itself. Once I have a final I will try to shed some weight but not much will be possible without compromising stiffness (the top back corner can easily shed some weight, the backplate can hardly be made thinner without loosing stiffness).

The nuts are hard to remove I am afraid. The back is only 3mm thick that would be all you get to hold the screws. I started with hot melt inserts but they come loose after only a few times dismantling (which I am doing as I am developping maybe this is not a general issue).

leesafur, 2021-12-18:
You're right about the daughterboard... I no longer need to put my fat fingers in there now that I have a load and unload button to use lol. I'm seriously considering moving the daughter board off the print head all together.

I trimmed up the fan shroud by 1mm on 3 sides and made the bolt holes smaller. It has about 30 hours on it now and is holding up well. The slicer had a hard time with the file as its hacked up pretty good now but I will attach it so you see what I did.

I'll go ahead and close this issue as original works as intended and wasn't a problem until I added a wiper bar at x252.
Thanks for all the work you've put into this as I now have a printer that prints petg flawless at 80-100mms with a draft quality at twice that speed
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
[Microswiss_Fan_Duct.zip](https://github.com/KoenVanduffel/CR-6_Strain_Gauge_Mounts/files/7739896/Microswiss_Fan_Duct.zip)

!

Closed 2021-12-18.

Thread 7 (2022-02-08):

Possible CAD file for microswiss

kritoke, 2022-02-08:
Not sure what the rights are on the case model, but stumbled across a microswiss one. Might help with the design markup. https://grabcad.com/library/microswiss-hotend-cr-10-2#!

leesafur, 2022-02-08:
Totally different from the CR6

kritoke, 2022-02-08:
It is close on most of it, but I guess the top part is a bit off. Thanks for your strain gauge setup for it.  Took me a little bit, but I got it working.  At some point I will probably do a write up on it once I got some hours in and address any issues that may come up. I really appreciate your hard work.

KoenVanduffel, 2022-02-08:
@kritoke I got the measurements of the MicroSwiss CR6 hotend from Ritchiedc based on which I made the mount. The CR10/ender3 version is quite a bit shorter and has a different coupler (dimensions might be the same though. I have not come across a cad model (nor made a model myself) so if you find one I can incorporate it even if only for the visuals.

Closed 2022-02-08.

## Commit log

2021-09-09 The hot end fan outlet was too small, replaced by a wider version
    [CR6 Dragon high flow & Orbiter mount V2.stl]
2021-09-09 clean up
    [5015 part fan mount for Dragon with rotated heater block V1.stl, 5015 part fan mount for Dragon with rotated heater block V2.stl, CR-6 Dragon & Orbiter mount M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]
2021-10-28 fan shroud updated with back plate cutout for some 5015 fan's
    [CR6 5015 part fan mount stock hotend.stl]
2021-11-28 Improved fan duct
    [31_mjolnir lwx latch_1x_SN_BN.stl, 5015 part fan mount for Dragon with rotated heater block V1.stl, 5015 part fan mount for Dragon with rotated heater block V2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]
2021-12-06 Dragon HF - Orbiter hotend fan Stator update
    hotend fan stator with minor update to avoid slicing issues with some slicers
2021-12-06 stock hotend V3 part fan mount
    [CR6 5015 part fan mount stock hotend.stl]
2021-12-11 Create CR6_Daughterboard mount to use with origianl daughterboard mount piece.stl
    [CR6_Daughterboard mount to use with origianl daughterboard mount piece.stl]
2021-12-18 Alternate mounting bracket
    Designed to bend around the X-motor pulley case and hold the daughterboard at 90 degrees to the carriage plate. Intended to be used to relocate the OEM daughterboard and its plastic case/LED holder. Some cables may be too short to use this mount if you discard the OEM case, and the LED will not illuminate the nozzle any more. Unless you have a BTT board, which signals "firmware flashing in process" with the LED, you may just want to remove the LED.
    [Right-Angled_Daughterboard_Bracket_v1.f3d, Right-Angled_Daughterboard_Bracket_v1.stl]
2021-12-18 Update README.md
    Added description of third (Right-Angled) daughterboard mount.
    Added caution that LED no longer positioned for illuminating the nozzle area, whichever board mount is used.
2022-01-02 Updated daughterboard mount and cable management
    Updated daughterboard mount and cable management
    [CR-6 Daughterboard mount V2.3mf, CR-6 Daughterboard mount V2.stl, CR-6 Ribbon cable clamp.stl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]
2022-01-22 Improved strain gauge frame support
    Improved the part of the mount resting on the strain gauge frame to avoid the Orbiter motor from levering on the strain gauge.
    [CR6_stock_hot_end_and_Orbiter_extruder_mount_V2.stl]
2022-01-24 Update README.md
    Missed a couple of errors in the previous edit.
2022-01-24 V4 Dragon Orbiter mount
    A connection on the left side is added to improve sturdyness along with making it compatible with both the standard and high flow Orbiters
2022-02-13 Move to PrusaPrinters
    This repo is being moved to PrusaPrinters.org as thats a more natural home for this sort of stuff.
    [5015 part fan mount for Dragon with rotated heater block V1.stl, CR-6 5015 part fan shroud.3mf, CR-6 5020 part fan shroud.3mf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]
2022-02-13 move to PrusaPrinters.org
    [CR-6_daughterboard_mount_V1.1.stl, CR6 Mosquito and Orbiter mount ot the strain gauge Injection molding inserts.stl, CR6 Mosquito and Orbiter mount ot the stra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]
2022-02-13 move to PrusaPinters.org
    [CR6 MicroSwiss hotend and Orbiter extruder M3 nut mounting.stl, CR6 MicroSwiss hotend and Orbiter extruder hot melt inserts.stl]
